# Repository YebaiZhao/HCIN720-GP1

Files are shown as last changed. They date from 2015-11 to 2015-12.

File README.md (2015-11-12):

# Group1 Assignment
For HCIN720 Group Assignment

## A description of the display, including pictures: 
 - Description of the display: Use [Magnetic Ferrofluid](http://www.amazon.com/gp/product/B008H40LG4?psc=1&redirect=true&ref_=oh_aui_detailpage_o01_s00) to display the due day from google calendar<br>
   1. The Wooden box: The box contains electrics and wires. Two layers of wood board are used to make the case to sustain the structure. 3D printed parts are screwed inside the box, holding the motor, magnets, Photon and other components.
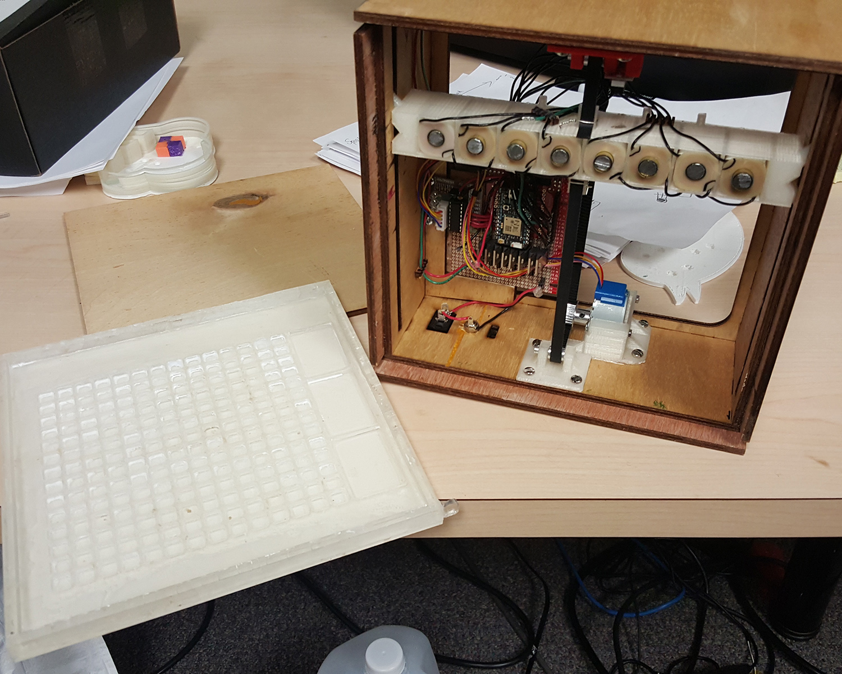
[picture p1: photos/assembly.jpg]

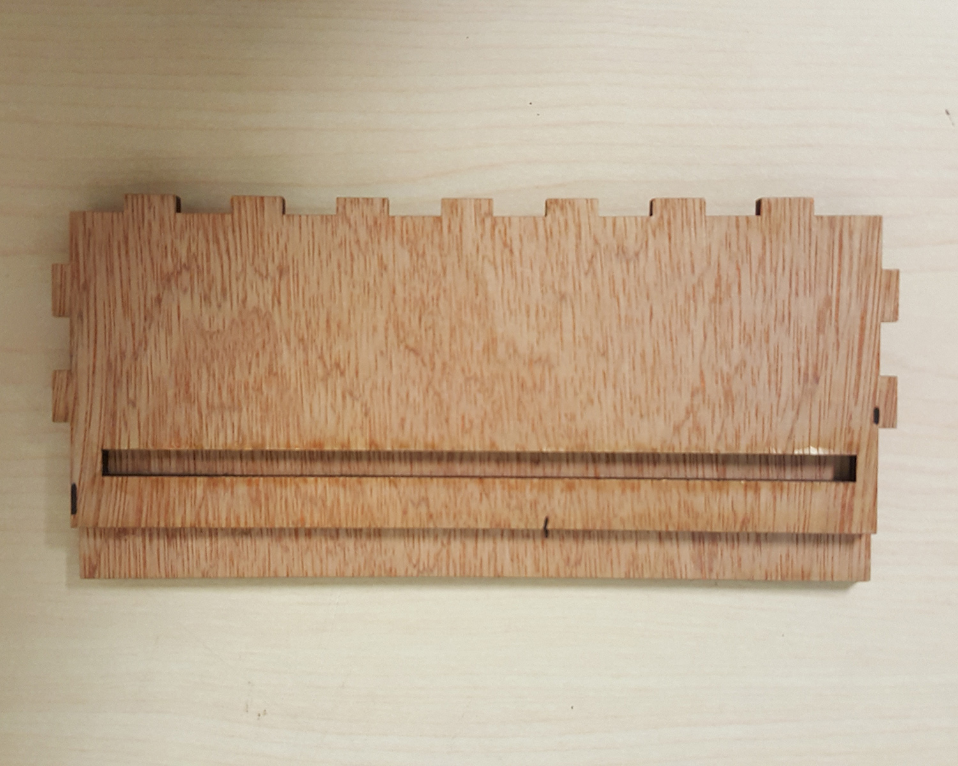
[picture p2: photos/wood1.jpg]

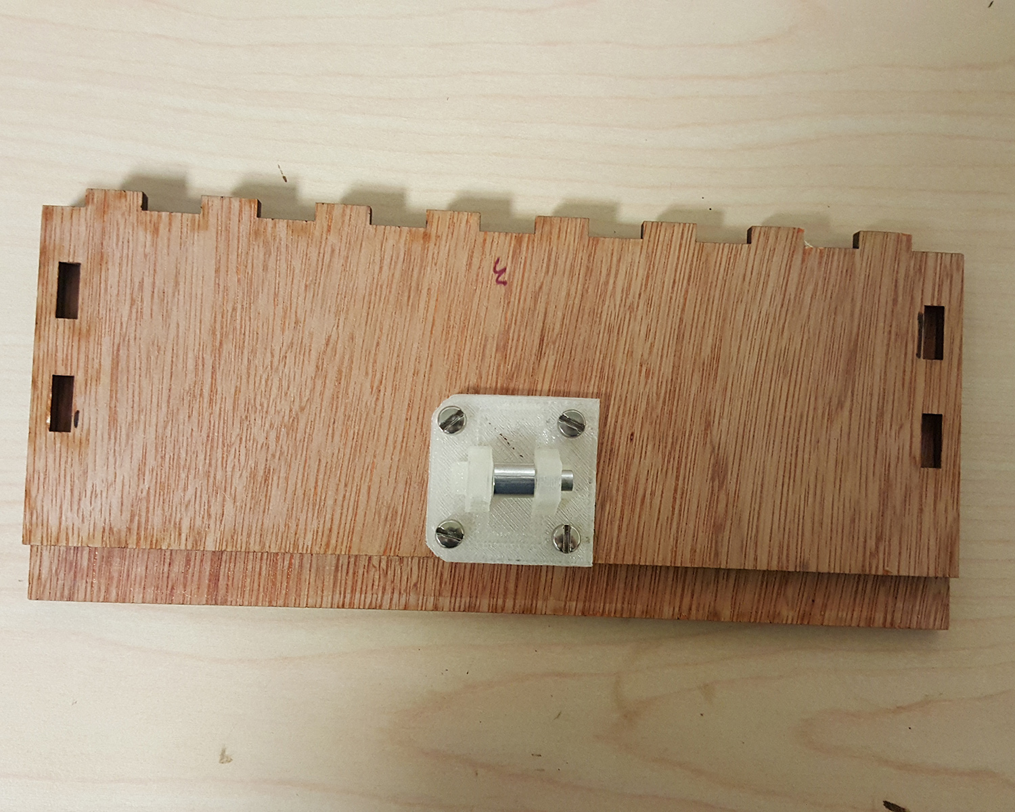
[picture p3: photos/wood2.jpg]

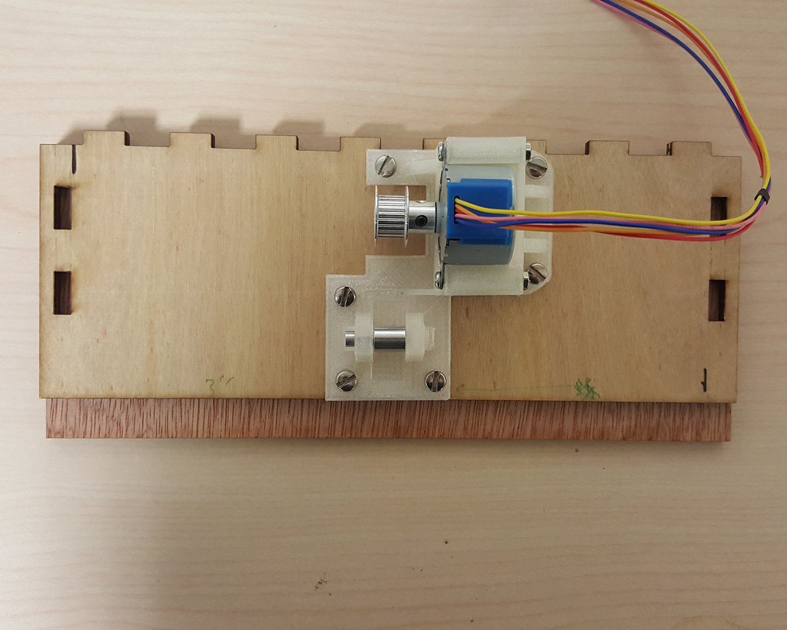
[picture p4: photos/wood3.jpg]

<br>
   2. Acrylic as basic container: We use Laser-cut acrylic as the container for the Ferrofluid. It has two layers, the first layer have a matrix (14*14) of holes and 3 big holes. The 14*14 matrix is used for display the number of days before the due day. 3 big holes act as storage for Ferrofluid. When there is a new calendar event created, Electromagnet will pull Magnetic Ferrofluid out from big holes into the matrix. Each small hole presents one more day left before the due.
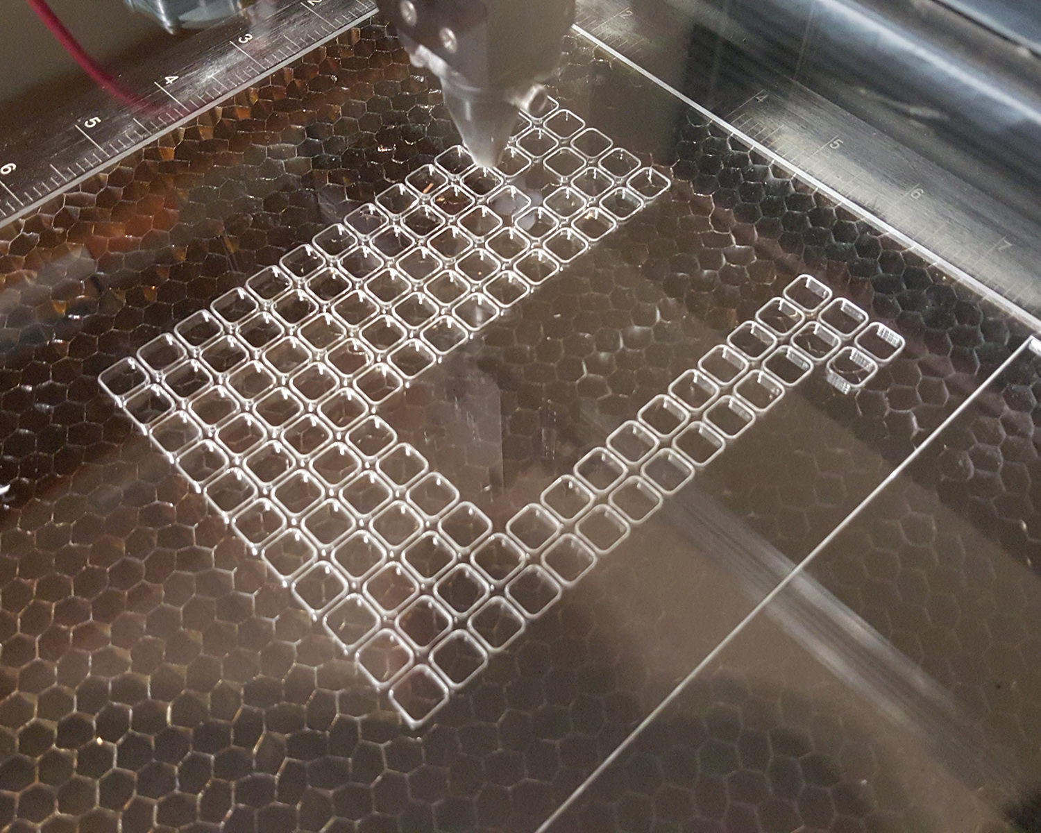
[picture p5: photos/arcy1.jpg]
<br>

   3. Aluminum cover on the top of acrylic: There is a layer of aluminum covering the acrylic to prevent acrylic from reaction to the solvent(Isopropyl alcohol).<br> 
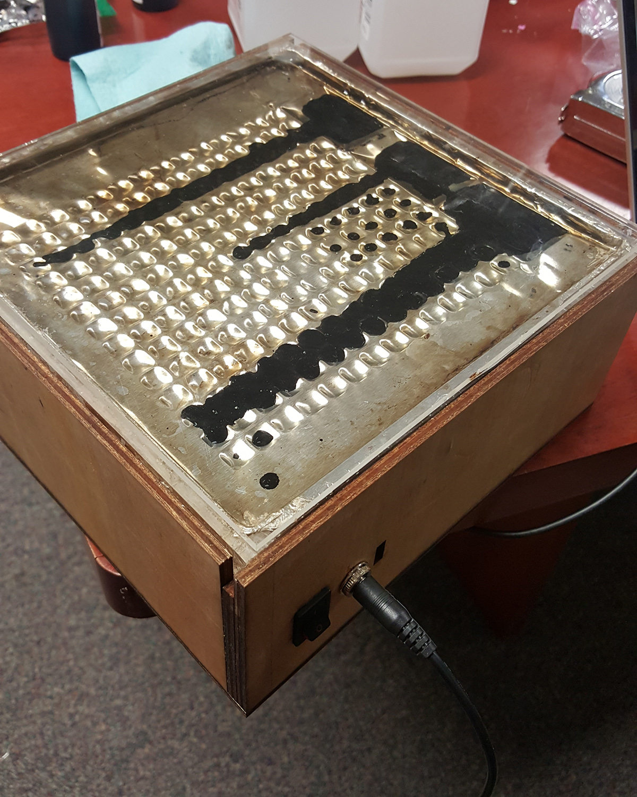
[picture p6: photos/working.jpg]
<br>

   4. Ferrofluid moving mechanism: There is an row of electromagnets, which pull the Ferrofluid out from the big tanks and fill appropriate small puddles. The motor is fixed on the side of the box to move the electromagnet carriage. The carriage will move to a specific location in order to create a new partten in the reservoir.<br>

   5. Circuit: We use P-channel MOSFETs to control the  5 volts driving power with the Photon's logic level signals. Diodes are also introduced to protect the circuit from induced current.
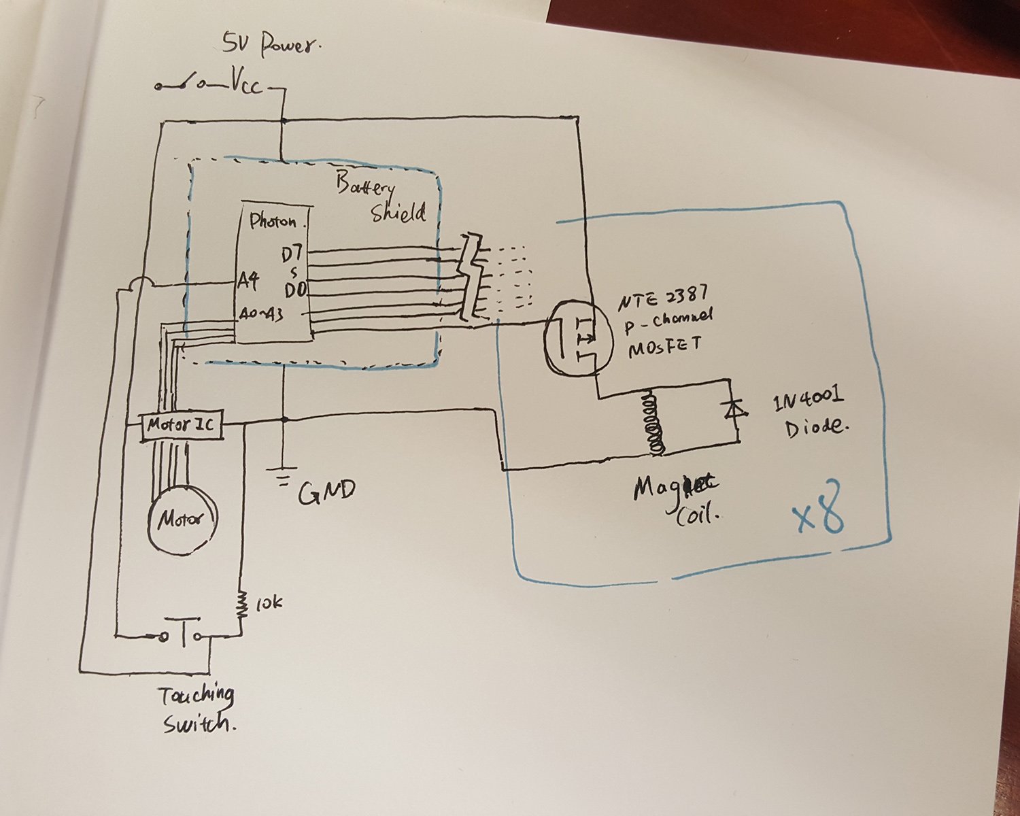
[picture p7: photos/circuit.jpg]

<br>

   6. summery: When you update one event on your google calendar, this display will probably changed based on its due day. It only contain event which is happened in 14 days, since there are only 14 hole a row. Everytime, this display only show most recent 3 events, according to the number of big holes.
   7. About the Ferrofluid and the container: We tried many combinations to create a stable container-liquid environment which the ferrofluid stays flexible and doesn't stick to anything else. But due to the limitation of time, money and our chemical knowledge, we are not able to make a satisfying container. This could be fixed if we later consult with the chemistry department of RIT.
  These are some of our test containers.
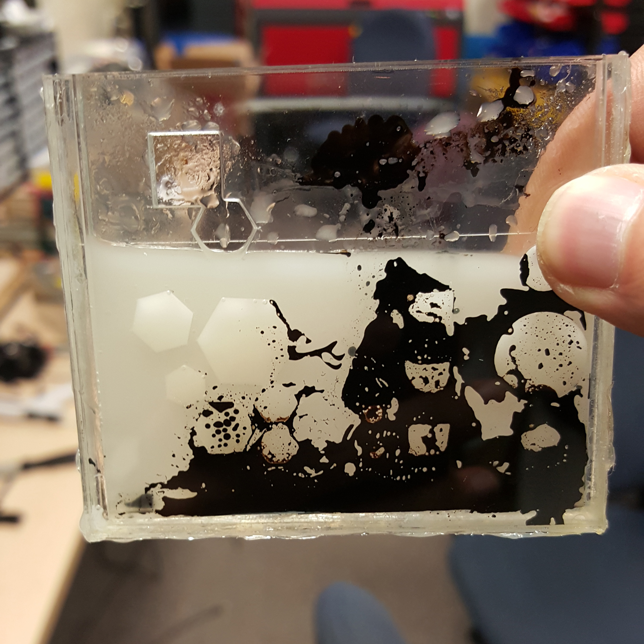
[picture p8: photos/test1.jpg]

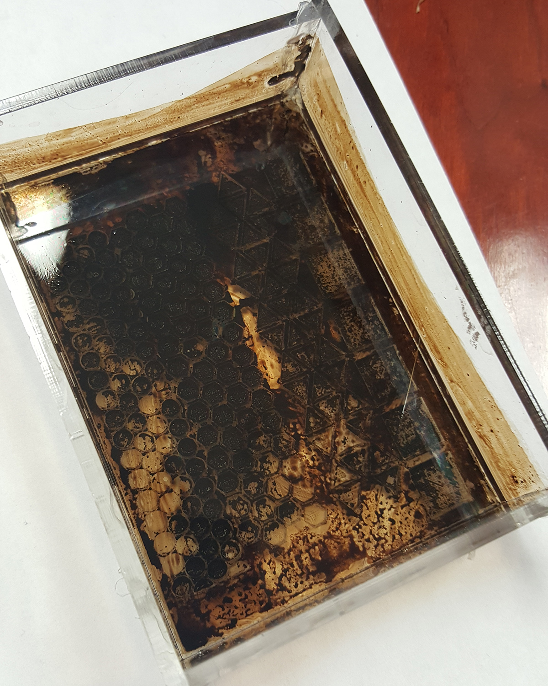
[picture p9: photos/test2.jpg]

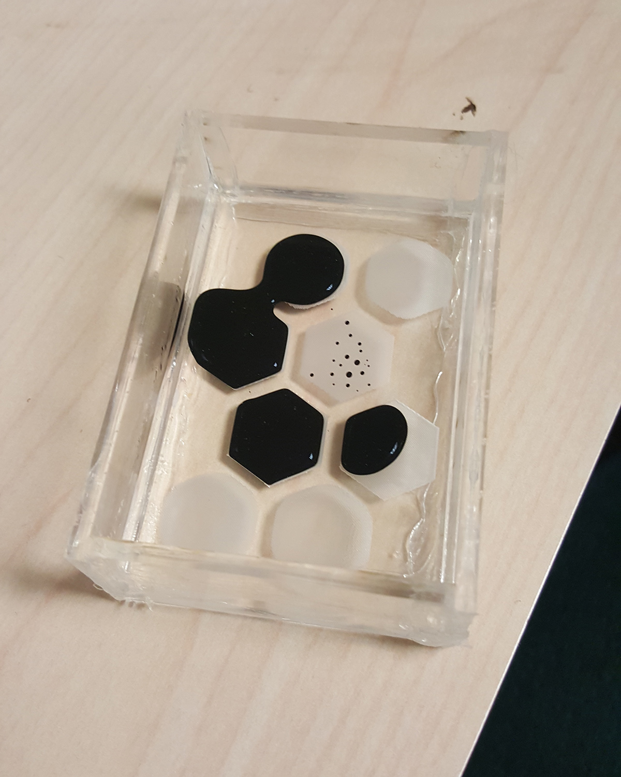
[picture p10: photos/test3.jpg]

 
## what choices you made for the information to display and the way you displayed it
 - choices made for information to display:<br>
   The most recent 14 days event<br>
   Only 3 events will be showing on the display<br>
 - The way displayed it: For each event, Magnetic Ferrofluid will be pull out to filled one row of small holes. The number of holes be filled present how many days left<br>
 
 - Here are some of our design sketches.
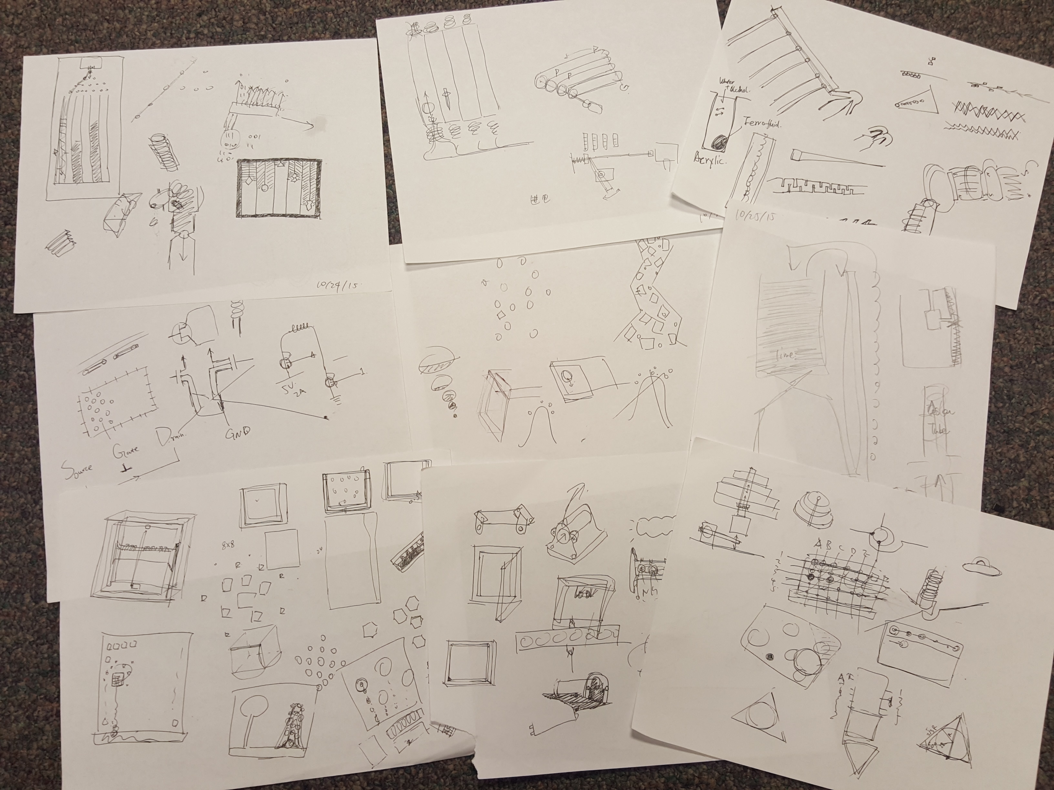
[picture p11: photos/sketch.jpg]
 - 

## Previous Research
 [SnOil](http://www.freymartin.de/en/projects/snoil) and [Ferriolic](http://www.ferrolic.com/) are two exmaples we found after we decided to work with Ferrofulid and electricmagent. We are trying to build our display with more flexbility and practicability than the predecessors that a clear image can stay with almost no power comsumption meanwhile we can change certain ferrofluid drop easily. We have confidence to believe that our work will be better in performance if we find the right solution-container combination. 

## source code and 3D/2D model files
 - The photon code in the photon folder, The GoogleCalendar code in googlecalendar foloer<br>
 - All the 3D and 2D model in the model foler
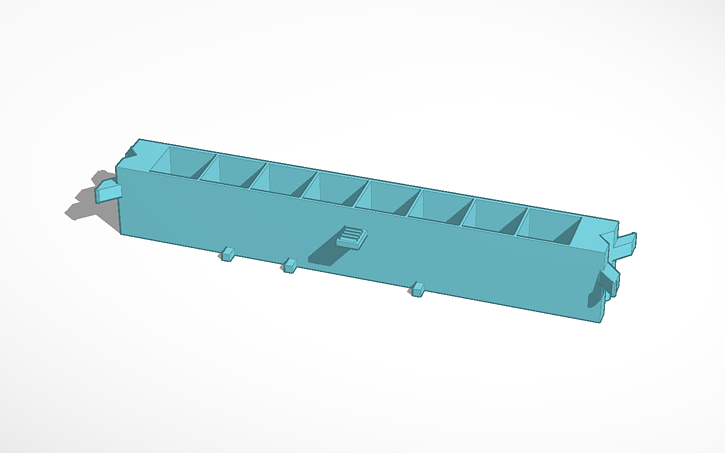
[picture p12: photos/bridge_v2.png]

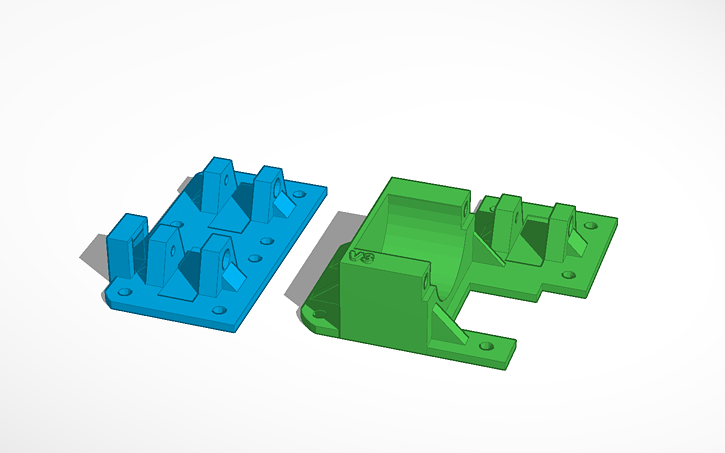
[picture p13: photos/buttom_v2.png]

<br>

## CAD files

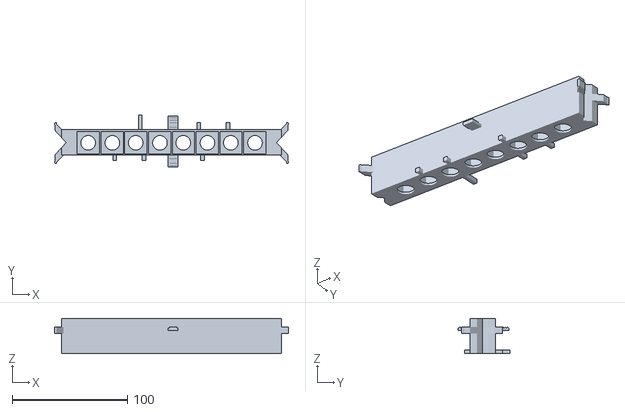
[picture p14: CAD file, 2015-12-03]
3D model/bridge_v2.stl
203.2 x 45.2 x 30.6

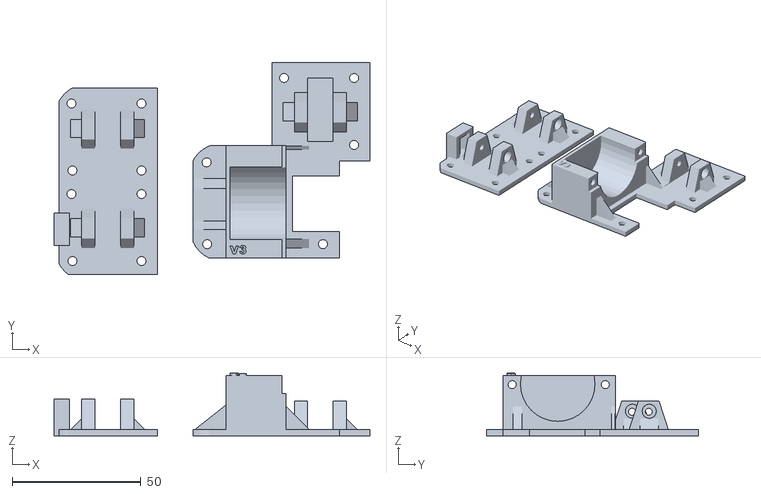
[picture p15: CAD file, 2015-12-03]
3D model/buttom_v2.stl
122.6 x 82.2 x 24.3

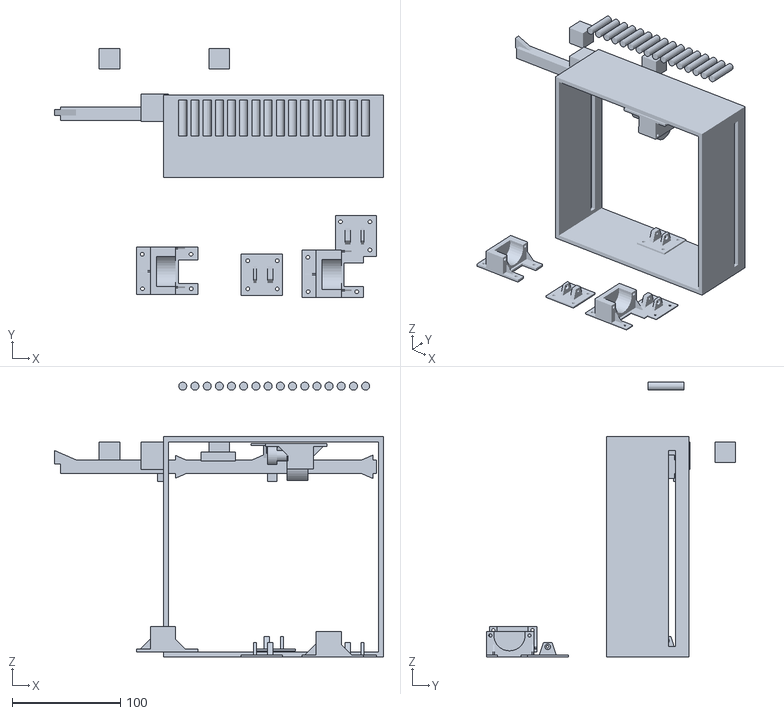
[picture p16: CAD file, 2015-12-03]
3D model/group01.stl
303.5 x 229.8 x 253.6

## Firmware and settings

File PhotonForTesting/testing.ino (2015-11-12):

int M1 = D0;
int M2 = D1;
int M3 = D2;
int M4 = D3;
int M5 = D4;
int M6 = D5;
int M7 = D6;
int M8 = D7;
int mPins[8] = {D0, D1, D2, D3, D4, D5, D6, D7};
int i;
int thisStep;
int eachStep;
int MOTOR1 = A0;
int MOTOR2 = A1;
int MOTOR3 = A2;
int MOTOR4 = A3;
int SWITCH1 = A4;


void setup()
{
  Serial.begin(9600);
  pinMode(D0, OUTPUT);
  pinMode(D1, OUTPUT);
  pinMode(D2, OUTPUT);
  pinMode(D3, OUTPUT);
  pinMode(D4, OUTPUT);
  pinMode(D5, OUTPUT);
  pinMode(D6, OUTPUT);
  pinMode(D7, OUTPUT);
  pinMode(D7, OUTPUT);

  pinMode(MOTOR1, OUTPUT);
  pinMode(MOTOR2, OUTPUT);
  pinMode(MOTOR3, OUTPUT);
  pinMode(MOTOR4, OUTPUT);
  // set the magnet pin to the high
  digitalWrite(D0, HIGH);
  digitalWrite(D1, HIGH);
  digitalWrite(D2, HIGH);
  digitalWrite(D3, HIGH);
  digitalWrite(D4, HIGH);
  digitalWrite(D5, HIGH);
  digitalWrite(D6, HIGH);
  digitalWrite(D7, HIGH);
}

void loop()
{
  //测试是否收到信号
    if (Serial.available())
    {
       inByte = Serial.read();
       state = int(inByte);
       Serial.println(state);
       if(state == 0){
         //move(8);
       }else if( state == 1){
         //move(-8);
       }else if (state == 49){
         //turnOnMag(0);
       }else if (state == 50){
         //turnOnMag(1);
       }else if (state == 51){
         //turnOnMag(2);
       }else if (state == 52){
         turnOnMag(3);
       }else if (state == 53){
         //turnOnMag(4);
       }else if (state == 54){
         //turnOnMag(5);
       }else if (state == 55){
         //turnOnMag(6);
       }else if (state == 56){
         //turnOnMag(7);
       }else if (state == 57){
         //turnOffMag(0);
       }else if (state == 58){
         //turnOffMag(1);
       }else if (state == 59){
         //turnOffMag(2);
       }else if (state == 60){
         //turnOffMag(3);
       }else if (state == 61){
         //turnOffMag(4);
       }
       else if (state == 62){
         //turnOffMag(5);
       }
       else if (state == 63){
         //turnOffMag(6);
       }else if (state == 64){
         //turnOffMag(7);
       }
    }

    /*if (accel.available())
    {
        accel.read();
        unsigned lightSensor = analogRead(A0);
        int x = accel.x;
        float cx = accel.cx;
        int y = accel.y;
        float cy = accel.cy;
        int z = accel.z;
        float cz = accel.cz;
        int click = 0;
        //int tap= accel.readTap();
        allLight(x);
        if(digitalRead(button) == HIGH)
        {
          click = 1;
        }

        sprintf(publishString1,"{\"sensor\":%u, \"cx\":%f, \"x\":%d, \"cy\":%f, \"y\":%d, \"cz\":%f, \"z\":%d, \"click\":%d, \"state\":%d}",lightSensor,cx,x,cy,y,cz,z,click,state);
        Serial.println(publishString1);
        if(selection == 1){
          Spark.publish("everything",publishString1);
        }else{
          Spark.publish("erase",publishString1);
        }
    }*/


}

void turnOnMag(int numberOfM){
    digitalWrite(mPins[numberOfM], LOW);
}

void turnOffMag(int numberOfM){
    digitalWrite(mPins[numberOfM], HIGH);
}

int move(int steps){
  //是正的时候向上移动， 负的时候向下移动
  //负的时候向没有开关的一边移动
  eachStep = 0;
  if(steps > 0){
    //向上 up
    eachStep = -1;
  }
  if(steps < 0){
    //向下 down
    eachStep = 1;
  }
  int thisStep;
  int i = 0;
  int steps_left = abs(steps);

  while(i < abs(steps)){
    i = i + 1;
    steps_left = steps_left + eachStep;
    thisStep = ( steps_left % 8 ) + 1;
    switch (thisStep) {
      case 1:
      //case 100:
      digitalWrite(MOTOR1, HIGH);
      digitalWrite(MOTOR2, LOW);
      digitalWrite(MOTOR3, LOW);
      digitalWrite(MOTOR4, LOW);
      //Serial.print(500);
      break;
      case 2:
      //case 100*2:
      digitalWrite(MOTOR1, HIGH);
      digitalWrite(MOTOR2, HIGH);
      digitalWrite(MOTOR3, LOW);
      digitalWrite(MOTOR4, LOW);
      //Serial.print(1000);
      break;
      case 3:
      //case 100*3:
      digitalWrite(MOTOR1, LOW);
      digitalWrite(MOTOR2, HIGH);
      digitalWrite(MOTOR3, LOW);
      digitalWrite(MOTOR4, LOW);
      //Serial.print(1500);
      break;
      case 4:
      //case 100*4:
      digitalWrite(MOTOR1, LOW);
      digitalWrite(MOTOR2, HIGH);
      digitalWrite(MOTOR3, HIGH);
      digitalWrite(MOTOR4, LOW);
      //Serial.print(2000);
      break;
      case 5:
      //case 100*5:
      digitalWrite(MOTOR1, LOW);
      digitalWrite(MOTOR2, LOW);
      digitalWrite(MOTOR3, HIGH);
      digitalWrite(MOTOR4, LOW);
      //Serial.print(2500);
      break;
      case 6:
      //case 100*6:
      digitalWrite(MOTOR1, LOW);
      digitalWrite(MOTOR2, LOW);
      digitalWrite(MOTOR3, HIGH);
      digitalWrite(MOTOR4, HIGH);
      //Serial.print(3000);
      break;
      case 7:
      //case 100*7:
      digitalWrite(MOTOR1, LOW);
      digitalWrite(MOTOR2, LOW);
      digitalWrite(MOTOR3, LOW);
      digitalWrite(MOTOR4, HIGH);
      //Serial.print(3500);
      break;
      case 8:
      //case 100*8:
      digitalWrite(MOTOR1, HIGH);
      digitalWrite(MOTOR2, LOW);
      digitalWrite(MOTOR3, LOW);
      digitalWrite(MOTOR4, HIGH);
      //Serial.print(4000);
      break;
    }
    delay(2);
  }
  return 1;
}
